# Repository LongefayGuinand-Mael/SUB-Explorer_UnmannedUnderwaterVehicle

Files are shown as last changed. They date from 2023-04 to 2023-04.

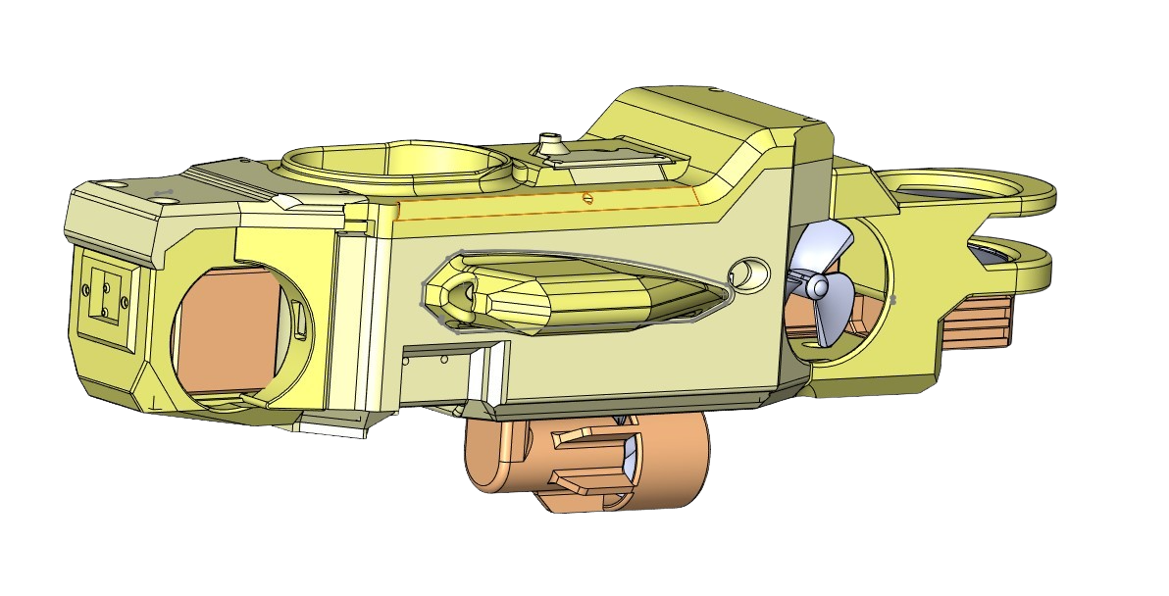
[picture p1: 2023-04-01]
UUV.png

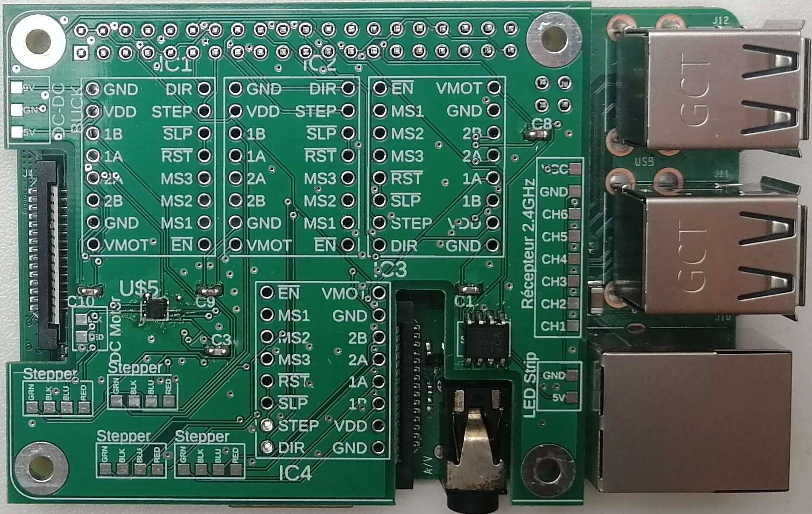
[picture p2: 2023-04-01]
SchémasÉlectroniques+PCB/Photos des PCB sur les Raspberry Pi/PCB Raspberry Pi 4B.jpg

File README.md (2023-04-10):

<br>
	<p align="center">
		<h1 align="center"> :warning:   WARNING   :warning: </h1>
	</p>
<br>

This project was made in French only for an Academic Work. So please consider that whole project files names, reports and other are only in French. This project was made during our last year in the ESME Sudria Engineering School between October 2022 and March 2023. 

Please note that this README.md is only a preface to all the work done during these 6 months of the project, if you wish to know more after reading this README, please refer to our report `/Rapports/Rapport Projet Drone Sous-Marin.pdf` (written in French).

------------------------------------------------------
------------------------------------------------------

<br>
	<p align="center">
	    <h1 align="center">Unmanned Underwater Vehicle - Sub-Explorer</h1>
	</p>
</br>

Dans le cadre de notre dernière année academic d'ingénierie à l'ESME Sudria (Master 2), mon groupe et moi-même avons travaillé pendant une durée de 6 mois sur un drone sous-marin ayant pour objectif principal la recherche scientifique. Dans le cadre de notre projet, nous avons mis en place diverses choses afin de mener à bien cet objectif et nous sommes arrivé à un résultat très concluant. Veuillez à noter que le README.md n'est qu'une préface à tout le travail effectué lors de ces 6 mois de projet, si vous avez pour souhait de d'en savoir plus après lecture de ce README, veuillez à vous référer à notre rapport `/Rapports/Rapport Projet Drone Sous-Marin.pdf`.

Ce projet c'est principalement articulé avec les parties suivantes :
- Définition du Cahier des charges 
- Veille technologique :
	- Recherche des Composants
	- Mise en place d'un schéma électrique
	- Réalisation des Printed Circuit Board
- Programmation (Python)
- Modélisation structurelle 3D du drone   
*Les autres parties (moins techniques) sont trouvables dans le rapport complet de notre projet de fin d'études.*

------------------------------------------------------

### Sommaire :
1. [Définition du Cahier des Charges](#cahier-des-charges)
2. [Choix des Composants](#choix-composants)
3. [Schémas Électroniques](#schémas-électroniques)
4. [Réalisation des Printed Circuit Board (PCB)](#pcb)
5. [Programmation](#programmation)
6. [Modélisation structurelle du drone](#modélisation-3d)
7. [Noms et Contacts des étudiants ayant travaillé sur le projet](#contacts)

------------------------------------------------------

<br>
	<p align="center">
	    <h2 align="center">Définition du Cahier des Charges</h2>
	</p>
</br>

### Introduction :
Notre objectif est de concevoir un drone sous-marin dans son intégralité, allant de la définition du cahier des charges à sa conception électronique et  3D. Pour mettre à bien notre projet, l'objectif premier est de mettre au point un système de pilotage efficace pour notre drone sous-marin, en veillant à sa motorisation directionnelle, à sa radiocommunication et à son design 3D. Nous prévoyons également d'intégrer des outils scientifiques à notre plateforme, ainsi que de travailler sur une optimisation de son design. En somme, ce projet est l'opportunité pour nous de mettre en pratique nos connaissances en matière de systèmes embarqués, tout en nous confrontant à des défis technologiques passionnants.
Dans le cadre de ce projet, nous mettons d’abord la priorité sur le pilotage de la plateforme (motorisation directionnelle, radiocommunication). Les outils scientifiques et l’optimisation du design seront vus dans un second temps.

### Fonctionnalités :
1. _Les fonctionnalités primaires :_
	- UUV manœuvrable sur 3 dimensions. → Motorisation directionnelle (lacet, tangage, profondeur, direction).
	- L’UUV est radiocommandé. → Conception d’un flotteur permettant de maintenir l’antenne (récepteur 2.4GHz) hors de l’eau afin de simplifier la communication entre le système de pilotage et la machine.
→ Utilisation d’une télécommande et d’un récepteur 2.4GHz.
	- Le drone doit être étanche afin de protéger le système de l’eau.
	- Le drone doit également répondre à une limite de taille afin qu'il puisse se déplacer dans des espaces restreints. Nous avons donc pour objectif de taille que le drone fasse maximum 600 mm de longueur et 300 mm de diamètre.
	- La flottaison de l’UUV doit être neutre : nous devons faire en sorte d’obtenir un équilibre entre le poids et la poussée d’Archimède du drone.
	- Nous voulons que le drone puisse effectuer des missions scientifiques d’une durée minimum de 30 minutes - 1 heure. Cela nous défini une contrainte d'autonomie.
2. _Les fonctionnalités secondaires :_
	- Retour vidéo (mise en place d’une caméra embarquée pour pouvoir voir ce qui se trouve dans l’environnement du drone même lorsque celui-ci n'est pas visible depuis la surface).
	- Système d’éclairage LED afin de pouvoir voir convenablement l’environnement où se trouve le drone via le retour caméra.
	- Capteurs de température et de pression (utile pour de la recherche et pour assurer le maintien structurel du drône en fonction de la pression exercée sur lui de part la pression de l’eau - liée à la profondeur à laquelle il se trouve).
	- Structure résistante aux chocs et protégeant les composants fragiles pouvant être exposés à l’extérieur du drone (par exemple les capteurs ou encore les hélices des moteurs).
3. _Les fonctionnalités intéressantes supplémentaires :_
	- Ajout de systèmes pour la collecte de données scientifiques : échantillonneur, sondeur, GPS, divers nouveau capteur, etc.
	- Intégrer une capacité de stockage et de récupération rapide des données.
	- Développement d’une application mobile pour le pilotage de tout le drone (contrôle de
son déplacement dans l’espace et des éléments scientifiques qu’il embarque et permettant l’affichage du flux vidéo en temps réel).

### Schéma Bloc Fonctionnel du Projet :

SchémaBlocFonctionel

------------------------------------------------------

<br>
	<p align="center">
	    <h2 align="center">Choix des Composants</h2>
	</p>
</br>

*Toutes les datasheets des composants utilisés sont regroupées dans les fichiers du projet dans le dossier `/DatasheetsComposents`.*

### Intelligences Numériques :
Nous utilisons dans ce projet 2 Raspberry Pi.   
- La première est une **Rasberry Pi 4B (de 4 à 8 Go RAM)**. Cette Raspberry Pi nous permet la réception des données envoyées par la télécommande et donc par l'utilisateur afin de contrôler les moteurs et l'allumage ou non des LED qu'il embarque.   
- La seconde est une **Raspberry Pi 3B+**. Cette Raspberry Pi, quant-à elle, nous permet d'éberger un WebServeur local afin d'avoir un retour caméra et capteurs (afin de connaître, même si nous ne voyons plus le drone depuis la surface, de connaître l'environnement dans lequel il est).

### Caméra Embarquée :
Comme dit plus haut, nous avons besoin de savoir consatemment l'environnement du drone même lorsque celui-ci n'est pas visible depuis la surface. Ainsi, nous utilisons une caméra embarquée dans le drone. Par soucis de simplicité et surtout de qualité, nous avons choisi de prendre la **Camera Module V2 Raspberry** (existe maintenant également avec un autofocus). Cette caméra embarqué nous permet d'avoir une excélente qualité (1280x720 pixel) avec un haut débit (jusqu'à 24 fps) et puis elle est nativement supportée par la Rasberry Pi 3B+ qui va l'utiliser et envoyer son stream vidéo sur le WebServeur qu'elle host.

### Récepteur Radio + Télécommande :
Dans notre projet, nous avons eu la volonté de contrôler notre drone à distance en imaginant un moyen d'éviter d'avoir un drone qui embarque un enrouleur de câble pour pouvoir communiquer avec l'utilisateur via ce qui s'apparente à un câble d'Arianne. Ainsi, nous avons choisi de mettre en place ce câble d'Arianne entre notre sous-marin et un flotteur. Ce flotteur pourra ainsi embarquer 2 antennes. L'une étant l'antenne radio (2.4GHz) et l'autre une antenne WiFi (dont nous reparlerons plus tard).

Nous avons donc prit un récepteur radio **FS-IA6B**. Ce récepteur 2.4GHz (fréquence laissée libre pour la science et d'autres recherche) va nous servirà communiquer avec notre sous-marin. En plus de ce récepteur, nous avons une télécommande FlySky (utilisée dans le modélisme et qui convient très bien à notre projet pour le moment). 

### Composants ayant un lien avec le déplacement du drone :
La phase la plus technique dans ce projet est le déplacement du sous-marin car en plus de la réception des données de la télécommande redio, il faut adapter les données récupérées en données fiables pour contrôler convenablement nos moteurs. 

Nous avons 2 types de moteurs : 
- 4 moteurs pas-à-pas **17HS08-1004S** commandé à l'aide d'un driver moteur **A4988-1182** par la Raspberry Pi 4B.
- 1 moteur à courant continu de la marque **lichifit** (utilisé dans le modélisme naval) commandé à l'aide d'un driver moteur **DRV8838** également par la Raspberry Pi 4B.

Les moteurs pas-à-pas seront utilisés pour des mouvements plus précis tels que les mouvements translatifs lattéraux et de profondeur et pour les mouvement rotatifs (lacet et tangage).    
Le moteur à courant continu sera quant-à lui utilisé uniquement pour la translation avant-arrière et sera notre propulseur principal.

### Composants ayant un lien avec la récupération de données (capteurs) :
Dans notre sous-marin, nous souhaiton à minima pouvoir récupérer deux données, la température et la pression. 

Pour le capteur de température, nous avons choisi le capteur **DS18B20**. Le choix de ce composant à été assez intuitif puisque celui-ci ressemble à une sonde, il est étanche et à une plage d'utilisation large avec une précision de 0.0625°C.

Pour le capteur de pression, nous avons choisi le capteur **MS5837-30BA**. Ce capteur fonctionne en I²C, il est étanche et a une plage de fonctionnement allant jusqu'à 30 bar (jusqu'à 290m de profondeur dans l'eau) avec une précision de 0.2mBar (soit ±2mm).

À l'avenir, nous imaginons pouvoir rajouter des capteurs tels que celui de salénité de l'eau et de pollution maritime ou encore un capteur de tangage pour la stabilisation du drone.

### Composants autres :
Les autres composants sont divers. 

Nous avons ici un convertisseur Buck-Boost **DFR0753** afin de pouvoir allimenter d'une tension de 5V les 2 Raspberry Pi mais d'une tension de 9V les différents moteurs et le bandeau LED.

En parlant du **bandeau LED**, nous avons imaginé embarquer des LED dans le sous-marin afin de permettre de les activer ou non pour pouvoir, en toutes circonstances et sur demande de l'utilisateur, de voir l'environnement de travail du drone sous-marin qu'il soit visible depuis la surface ou pas. Le bandeau LED est unicolore blanc, certifié IP67 (étanche poussière et eau), et peut être allimenté jusqu'à 12V. Nous l'utilisons avec une tension d'allimentation de 9V largement suffisante pour nous.

------------------------------------------------------

<br>
	<p align="center">
	    <h2 align="center">Schémas Électroniques</h2>
	</p>
</br>

*Pour une meilleure qualité, les images des schémas électroniques sont trouvables dans les fichiers du projet dans le dossier `/SchémasÉlectroniques+PCB`) Leurs noms étants : `Schéma Électronique - Raspberry Pi 3B+.png` et `Schéma Électronique - Raspberry Pi 4B.png`.*

Après l'analyse de tous les composants, nous avons mis en place 2 schémas électroniques. L'un concerne la Raspberry Pi 3B+ et l'autre la Raspberry Pi 4B.

### Partie Raspberry Pi 3B+ :

Pour cette partie, nous retrouvons dans le schéma électronique les capteurs de température et de pression. Il est à noté également que nous avons de géré par cette Raspberry Pi la caméra embarquée.

Schéma Électronique - Raspberry Pi 3B+

### Partie Raspberry Pi 4B :

Pour cette partie, nous retrouvons dans le schéma électronique les 4 moteurs pas-à-pas ainsi que leurs drivers respectifs, le moteur à courant continu et son driver, le bandeau LED, le récepteur 2.4GHz et des pins de branchement pour le convertisseur Buck-Boost (9V à 5V). 

Schéma Électronique - Raspberry Pi 4B

***À Noter :*** *Les fichiers Fusion360 ayants permis de faire les schémas électroniques ainsi que les PCB sont trouvables dans les fichiers du projet dans le dossier `/SchémasÉlectroniques+PCB/FichiersFusion`.*

------------------------------------------------------

<br>
	<p align="center">
	    <h2 align="center">Réalisation des Printed Circuit Board (PCB)</h2>
	</p>
</br>

*Fichiers de conception des PCB sont trouvables dans les fichiers du projet dans le dossier `/SchémasÉlectroniques+PCB/FichiersConceptionPCB`. Un dossier regroupe les fichiers utiles par un fabriquant de PCB pour faire celui de la Raspberry Pi 3B+ et un autre dossier est pour celui de la Raspberry Pi 4B.*

Cette partie ne pourra pas être beaucoup développée à l'écrit. Pour faire au plus simple, suite à la mise en place de nos 2 schémas électroniques, nous avons pu mettre en place 2 PCB qui seront utilisés pour notre projet (un pour chacune des intelligences électroniques). Sur le PCB de la Raspberry Pi 3B+ on peut y retrouver les branchements des différents capteurs tandis que sur le PCB de la Raspberry Pi 4B on y retrouve tous les composants utiles pour la réceptions des commandes de l'utilisateurs et les différents systèmes et branchements pour les moteurs et bandeau LED (en outre, tout ce qui est contrôllable par l'utilisateur à distance). 

La seconde chose importante mise en place est la définition de contraintes de dimentionnement afin de permettre aux 2 PCB de se brancher directement sur les Raspberry Pi. Ces contraintes sont principalement liée aux composants internes des Raspberry Pi et leurs hauteurs qui peuvent être génantes (dans les grandes lignes, ça regroupe les composants tels que celle du port éthernet, des ports USB, port de branchement caméra, port Jack et HDMI).

***Rappel :*** *Les fichiers Fusion360 ayants permis de faire les schémas électroniques ainsi que les PCB sont trouvables dans les fichiers du projet dans le dossier `/SchémasÉlectroniques+PCB/FichiersFusion`.*

------------------------------------------------------

<br>
	<p align="center">
	    <h2 align="center">Programmation (Python)</h2>
	</p>
</br>

*Tous les fichiers de programmation sont regroupées dans les fichiers du projet dans le dossier `/Programmation/Code`. Dans ce dossier on peut y retrouver les codes en Python (`.py`) ainsi que des logigrammes des programmes (au format `.png`).* 

Pour commencer, nous avons 2 intelligences numériques (1 Raspberry Pi 3B+ & 1 Raspberry Pi 4B) qui vont fonctionner simultannément mais de manière totalement distincte l'une de l'autre. Ainsi, nous exposons ci-dessous les logigrammes des programmes des 2 intelligences numériques : 

### Partie Raspberry Pi 3B+ :

Logigramme Raspberry Pi 3B+ - SUB-Explorer

Nous pouvons retrouver 2 étapes, l'initialisation et le fonctionnement. L'initialisation nous permet d'instancier les divers pins de la Raspberry que nous utilisons par la suite dans notre code ainsi que les multiples librairies utilisées. La phase de fonctionnement permet l'hébergement et l'envoie du stream de la caméra embarquée sur le WebServeur local de la Raspberry Pi 3B+. Il sera possible par la suite de créer un multi-thread afin de pouvoir récupérer en parallèle du WebServeur des données de capteurs pour les ajouter au retour caméra sur la page Web hébergée (*un début de code dans ce sens est retrouvable sous le nom `TempPrint_CameraWebLocal.py`*).

### Partie Raspberry Pi 4B :

Logigramme Pi4B (1) - SUB-Explorer

Tout comme pour la Raspberry Pi 3B+, nous pouvons y voir qu'il y a 2 étapes dans ce logigramme, l'initialisation et le fonctionnement en temps-réel avec la mise en place d'un multi-thread ce qui équivaut à l'utilisation de plusieurs coeurs du processeur de la Raspberry Pi 4B qui se charge de ce code. *On peut également retrouver le programme de récupération des données réceptionnées depuis la télécommande radio sur le logigramme `Logigramme Pi4B (2) - SUB-Explorer.png` mit dans le fichier `/Programmation/LogigrammesExplicatifs/`.*

------------------------------------------------------

<br>
	<p align="center">
	    <h2 align="center">Modélisation Structurelle du Drone</h2>
	</p>
</br>

Voici une image de l'assemblage total des pièces imprimées en 3D de notre drone : 

UUV

*Pour une meilleure qualité, l’image de l'assemblage de la modélisation structurelle du drone sont trouvables dans les fichiers du projet (au niveau de la racine). Son nom étant : `Assemblage3D.png`.*   

Voici également une vidéo montrant l'**ordre assemblage des quelques 28 pièces (_vis non-incluses_)** composants notre sous-marin : 

https://user-images.githubusercontent.com/80823327/229296633-9bad1075-d35f-4a4c-87c2-66e0a59497dc.mp4
   
**Concernant les fichiers 3D de chacune des pièces ainsi que de l'assemblage, ces fichiers sont trouvables dans les fichiers du projet dans le dossier `/Modélisation3D`.**

------------------------------------------------------

<br>
	<p align="center">
	    <h2 align="center">Noms et Contacts</h2>
	</p>
</br>


 
 

-------------------------------------
-------------------------------------
## License
***© COPYRIGHT - All Rights Reserved - Zapata Industry (LONGEFAY-PIOT-POPESCO)***  
***Important :*** *Afin de poursuivre le projet, merci de nous contacter sur LinkedIn pour avoir notre approbation.*

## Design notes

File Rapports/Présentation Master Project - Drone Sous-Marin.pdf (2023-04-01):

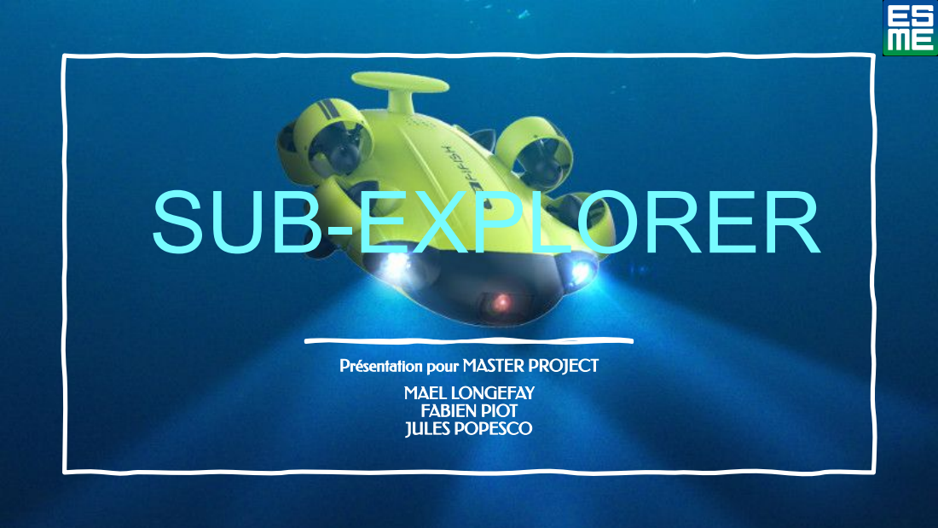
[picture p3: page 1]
SUB-EXPLORER; MAEL LONGEFAY FABIEN PIOT JULES POPESCO

Présentation pour MASTER PROJECT

# Sa mission :

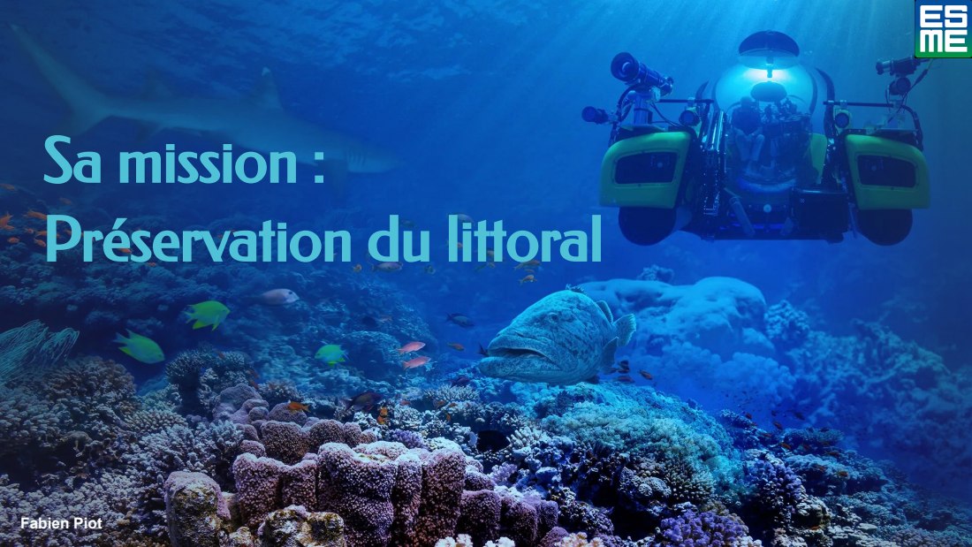
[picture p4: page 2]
Fabien Piot

Préservation du littoral

# Découvrez le drone sous-marin SUB-Explorer

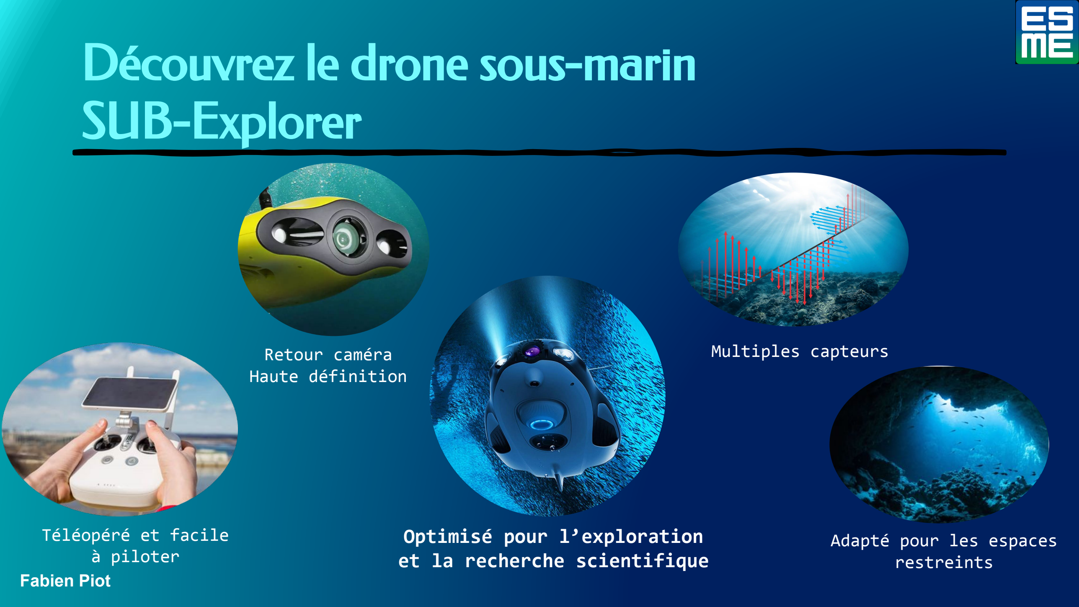
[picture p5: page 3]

Optimisé pour l’exploration et la recherche scientifique

Adapté pour les espaces
restreints

Téléopéré et facile
à piloter

Retour caméra
Haute définition

Multiples capteurs

Fabien Piot

# SUB-Explorer c’est également …

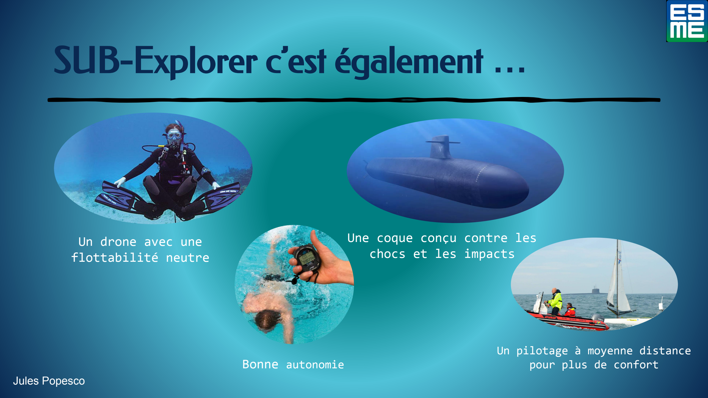
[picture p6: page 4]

Un drone avec une
flottabilité neutre

Bonne autonomie

Une coque conçu contre les chocs et les impacts

Un pilotage à moyenne distance pour plus de confort
Jules Popesco

# Voici à quoi ressemble notre prototype

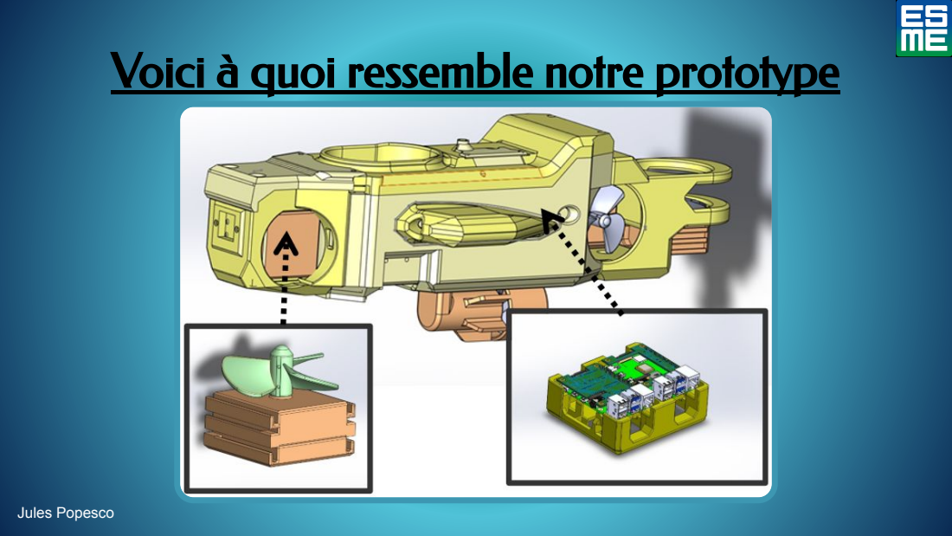
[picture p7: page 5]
Jules Popesco

# Montage du prototype

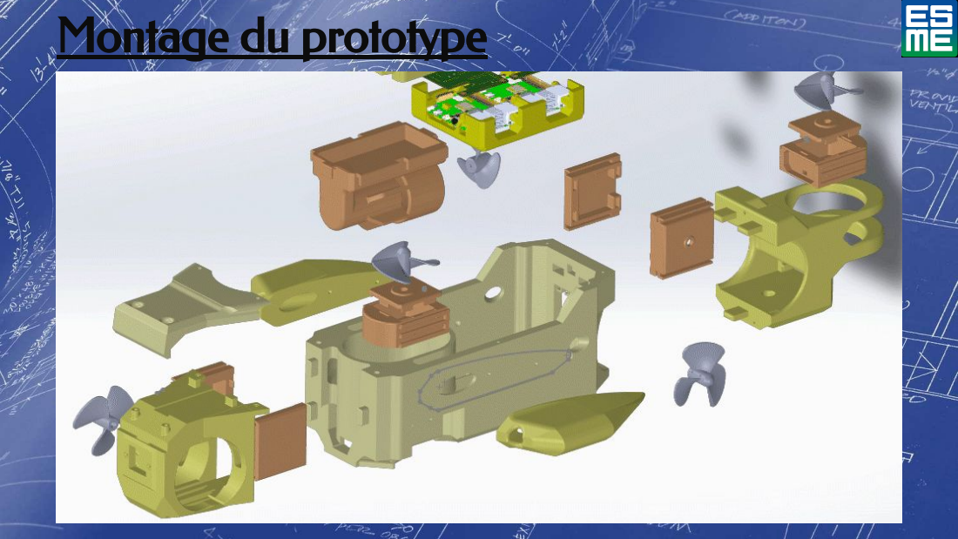
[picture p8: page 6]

# La force de SUB-Explorer : Sa grande modularité

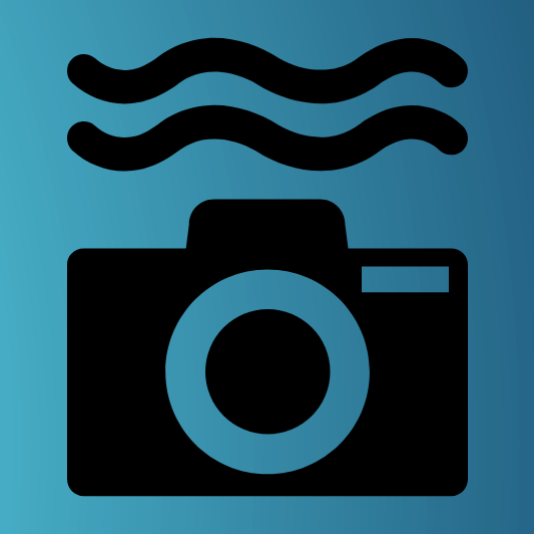
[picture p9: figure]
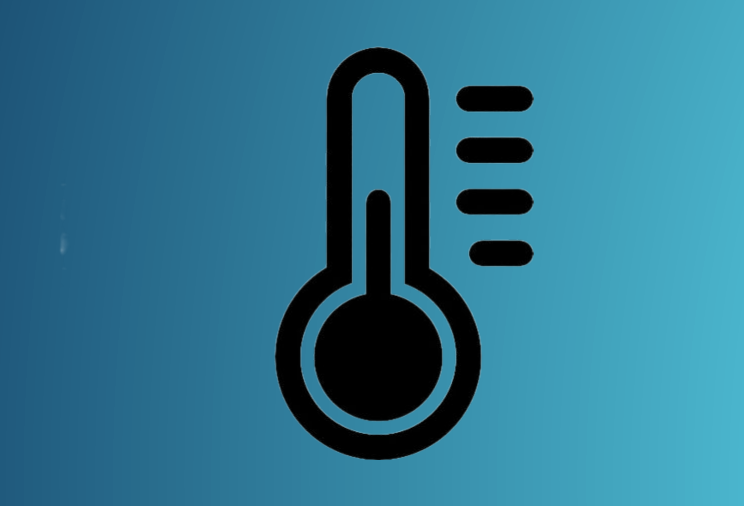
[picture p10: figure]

Plusieurs modules embarqués :

- caméra embarqué haute définition
- capteur de température

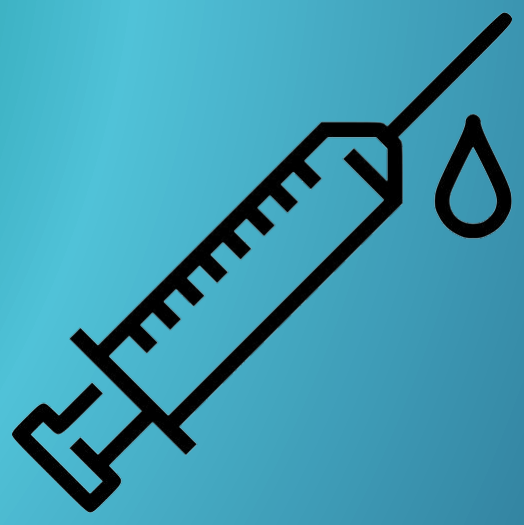
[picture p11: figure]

- capteur de pression

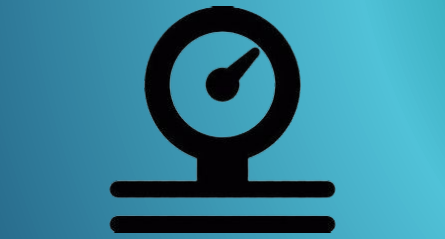
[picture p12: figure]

- module d'échantillonnage
- un éclairage LED

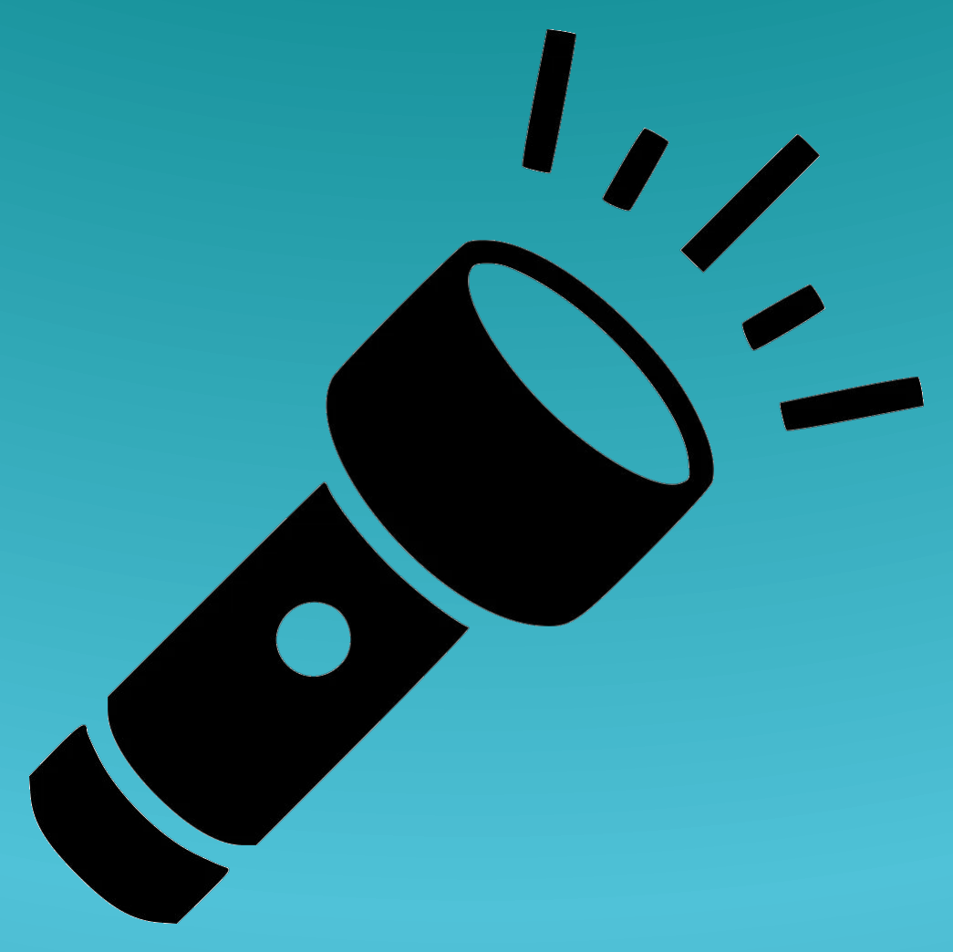
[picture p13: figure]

Mael LONGEFAY

# L’avenir de SUB-Explorer

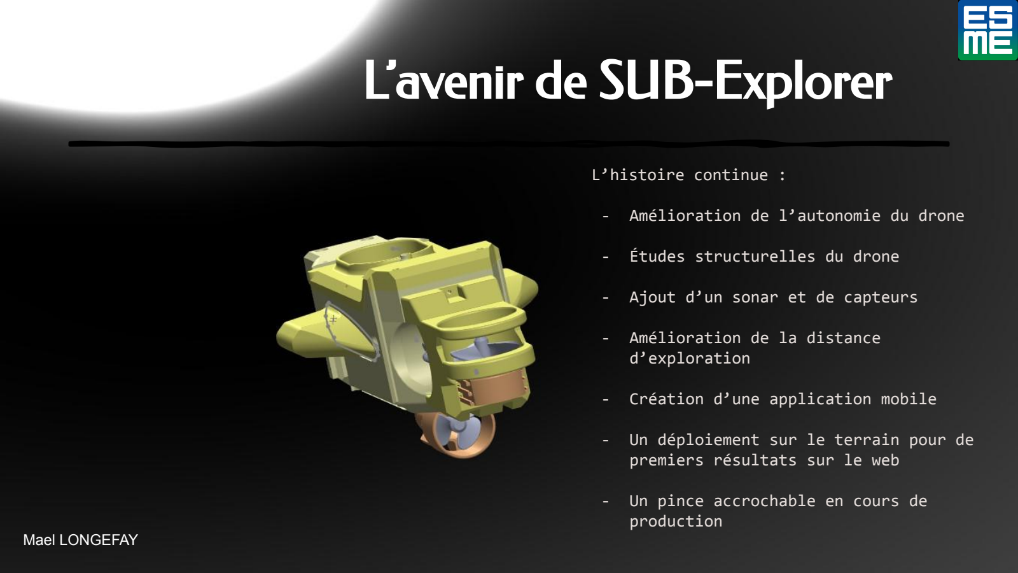
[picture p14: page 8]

L’histoire continue :

- Amélioration de l’autonomie du drone
- Études structurelles du drone
- Ajout d’un sonar et de capteurs
- Amélioration de la distance d’exploration
- Création d’une application mobile
- Un déploiement sur le terrain pour de premiers résultats sur le web
- Un pince accrochable en cours de production
Mael LONGEFAY

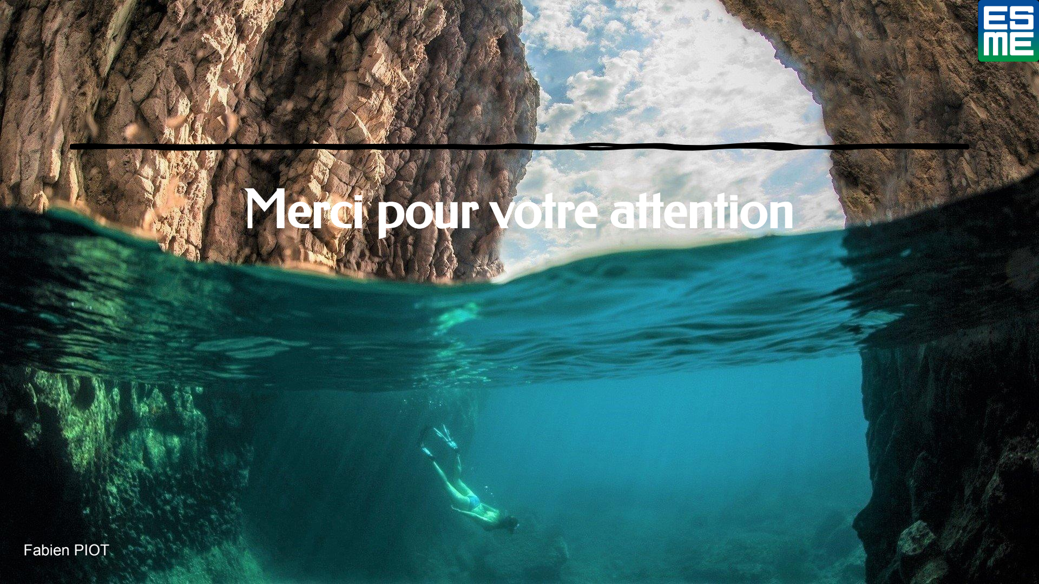
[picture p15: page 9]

# Merci pour votre attention

Fabien PIOT

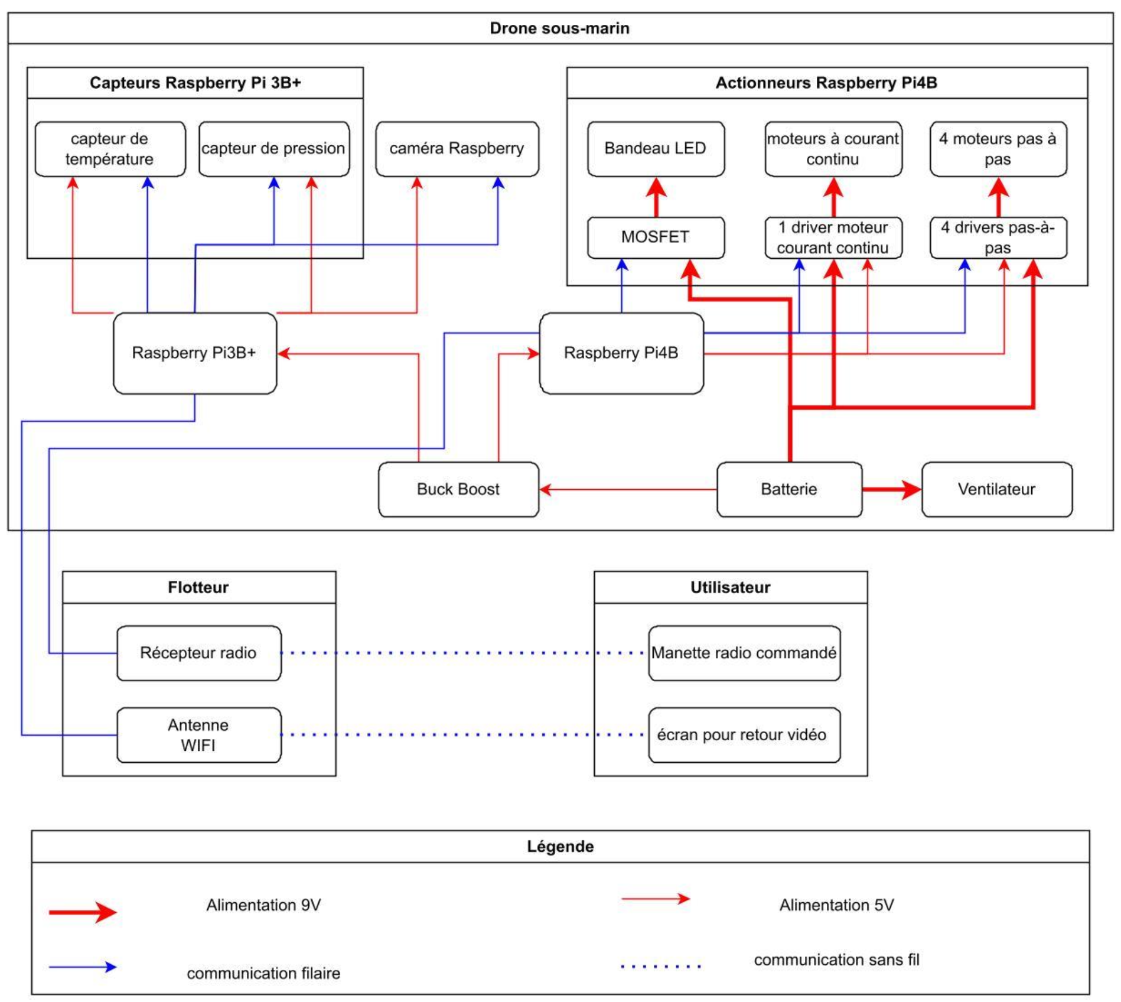
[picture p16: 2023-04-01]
SchémaBlocFonctionel.png

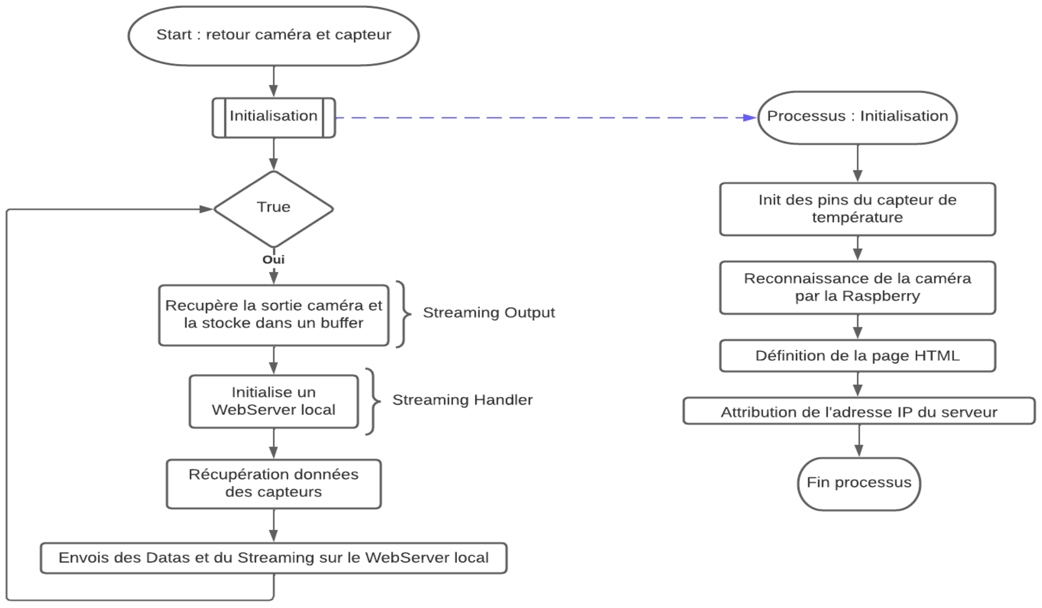
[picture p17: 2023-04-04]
Programmation/LogigrammesExplicatifs/Logigramme Raspberry Pi 3B+ - SUB-Explorer.png

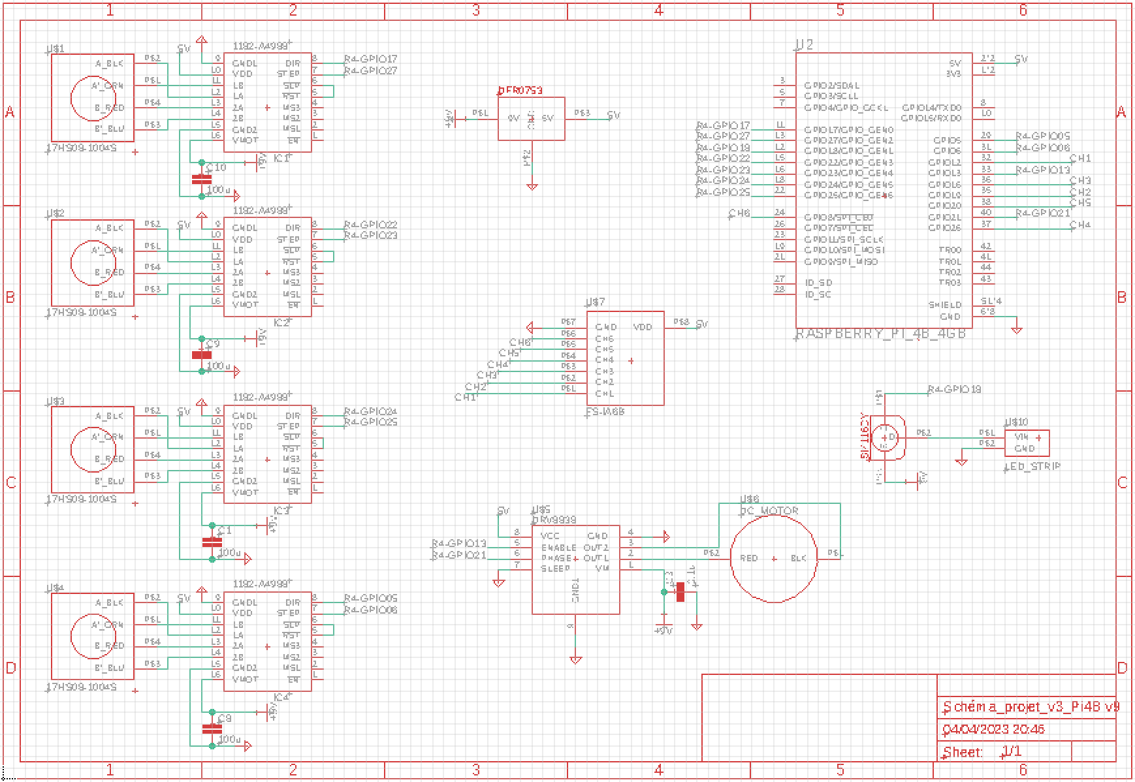
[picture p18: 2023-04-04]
SchémasÉlectroniques+PCB/Schéma Électronique - Raspberry Pi 4B.png

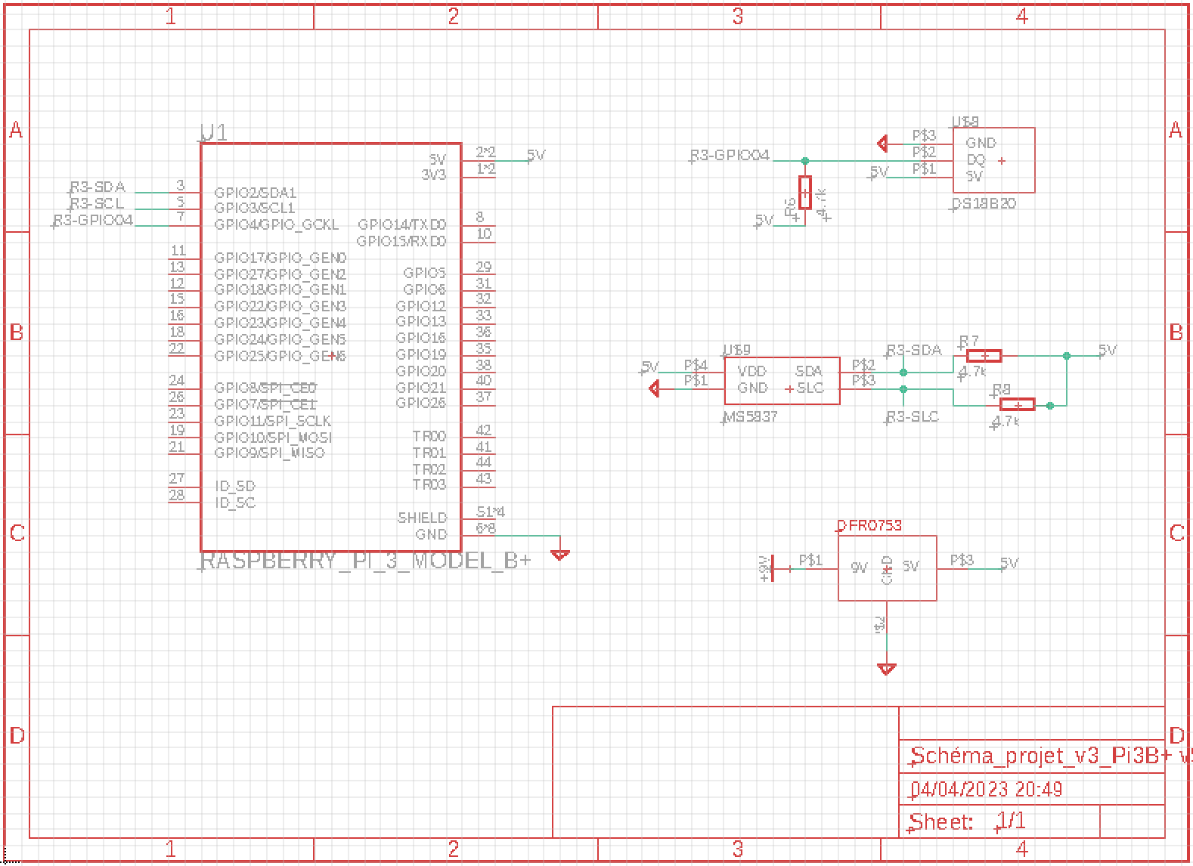
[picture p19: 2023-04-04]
SchémasÉlectroniques+PCB/Schéma Électronique - Raspberry Pi 3B+.png

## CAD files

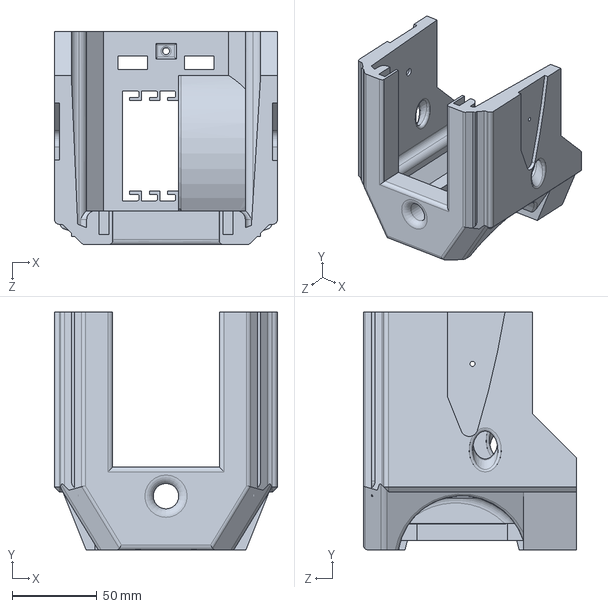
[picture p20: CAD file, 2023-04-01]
Modélisation3D/CoqueMain2.sldprt
131.8 x 140.5 x 126.0 mm

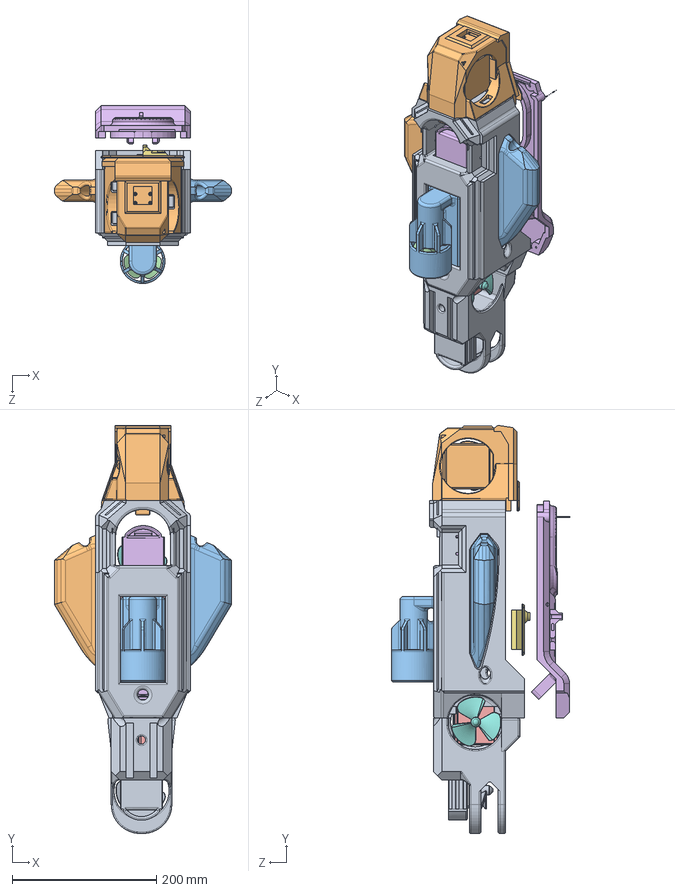
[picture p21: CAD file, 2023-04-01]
Modélisation3D/Assemblage1.sldasm
245.8 x 565.2 x 246.8 mm
CoqueMain
Aile
AileGauche
blk_steplarge_under
blk_steplarge_upper
bloc_moteur_step_under
bloc_moteur_step_upper
Helice x 2
Blk_ariere
Blk_avant
bloc_moteurCC
Helice DC
Etagère
Couverclehull
Couverclehull_ant

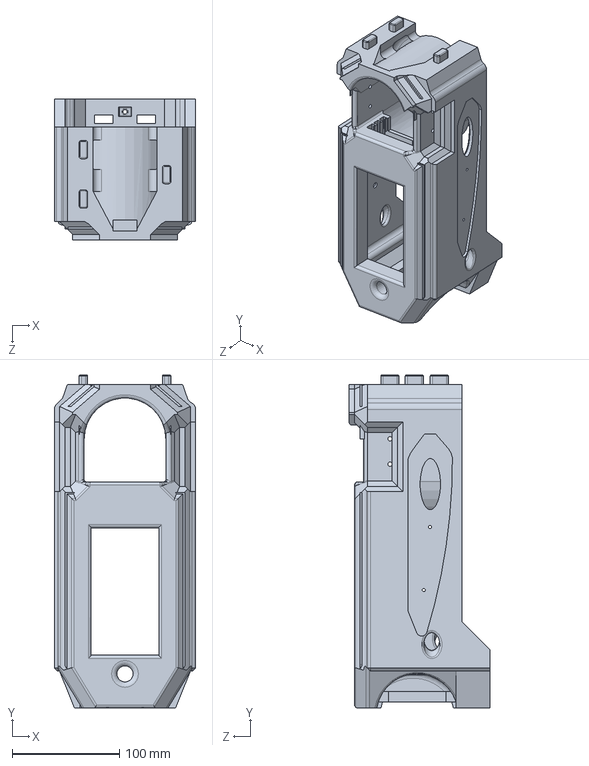
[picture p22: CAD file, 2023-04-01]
Modélisation3D/CoqueMain.sldprt
131.8 x 310.2 x 131.0 mm

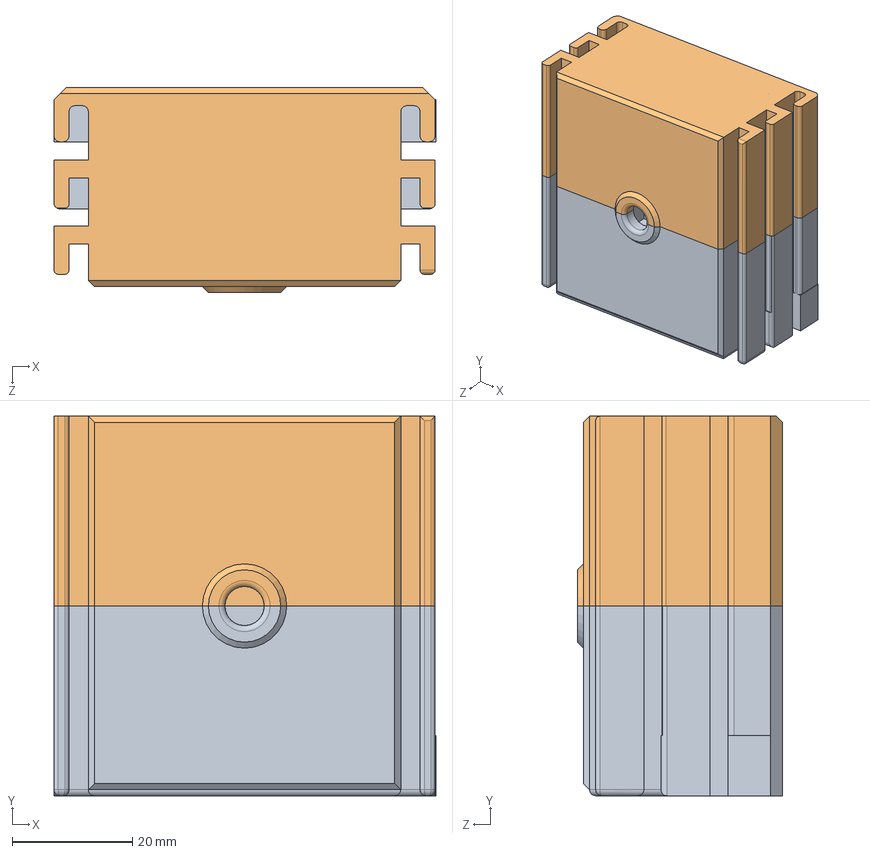
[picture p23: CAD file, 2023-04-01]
Modélisation3D/Stepmotlarge.sldasm
63.4 x 63.0 x 34.0 mm
blk_steplarge_upper
blk_steplarge_upper2

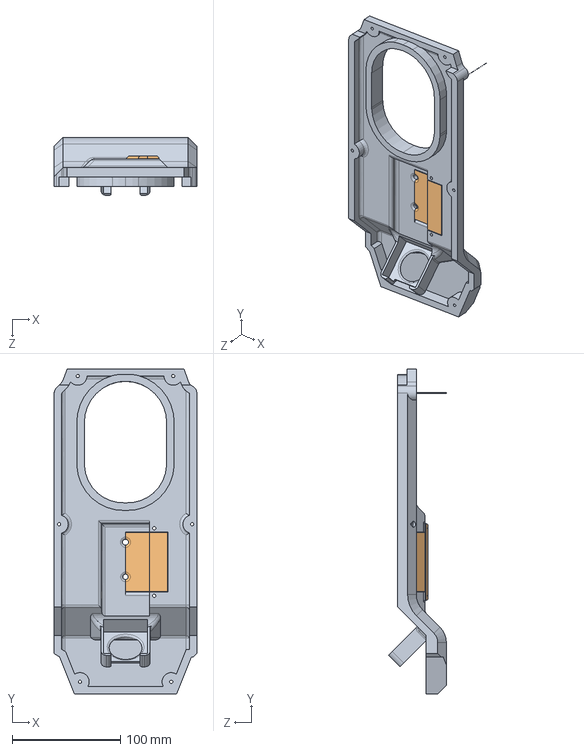
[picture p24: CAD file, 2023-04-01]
Modélisation3D/Assemblage2.sldasm
131.8 x 300.2 x 53.4 mm
Couverclehull
Couverclehull_ant

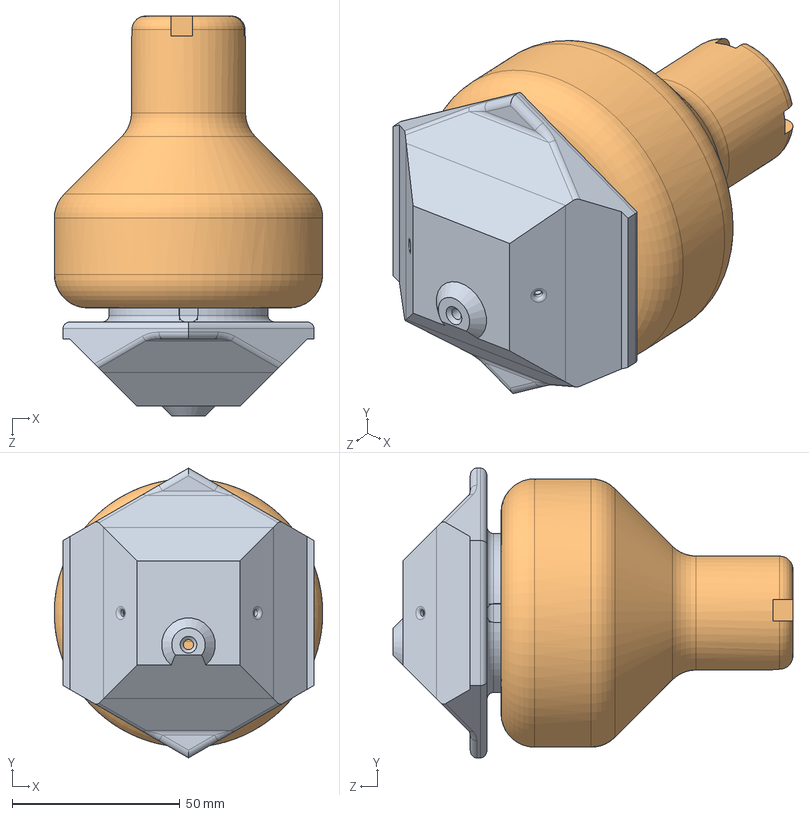
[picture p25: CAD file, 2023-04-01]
Modélisation3D/FlotteurAssemblage.sldasm
80.0 x 86.3 x 119.2 mm
Couvercle flotteur
Flotteur2

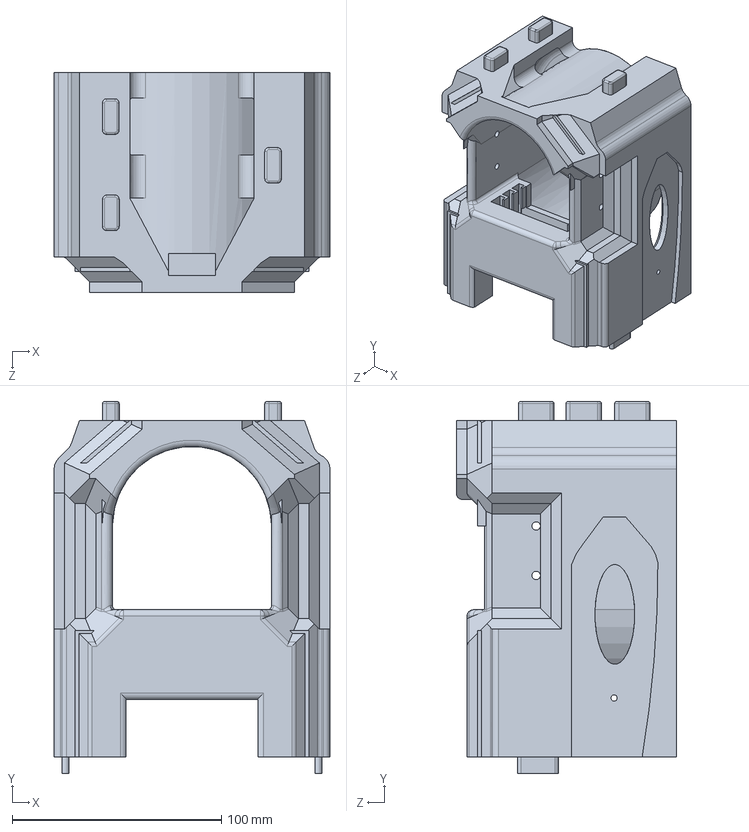
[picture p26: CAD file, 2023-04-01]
Modélisation3D/CoqueMain1.sldprt
131.8 x 177.7 x 105.0 mm

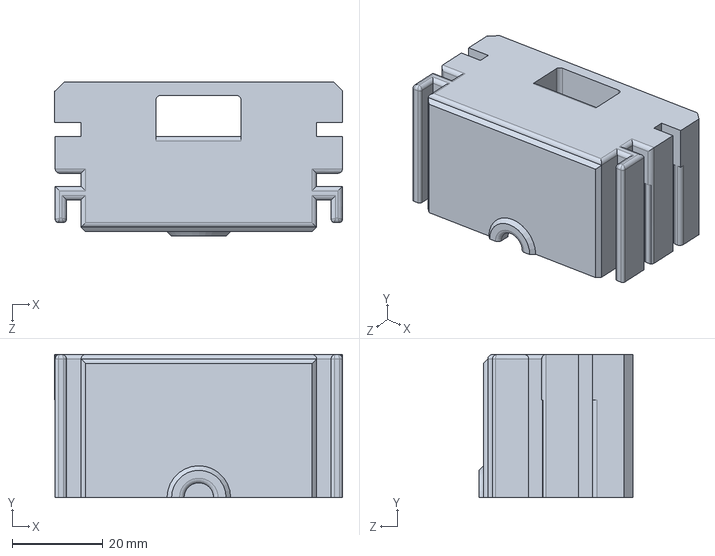
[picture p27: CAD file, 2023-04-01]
Modélisation3D/NewBLK.sldprt
63.4 x 31.5 x 34.0 mm

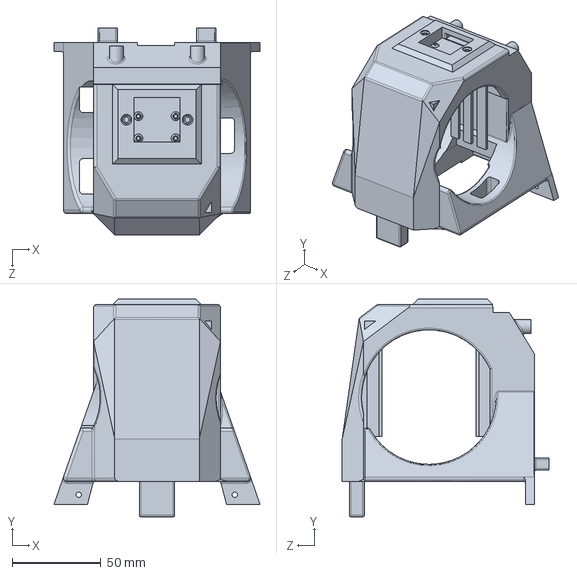
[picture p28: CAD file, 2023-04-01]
Modélisation3D/CoqueAvant.sldprt
116.3 x 123.0 x 116.7 mm

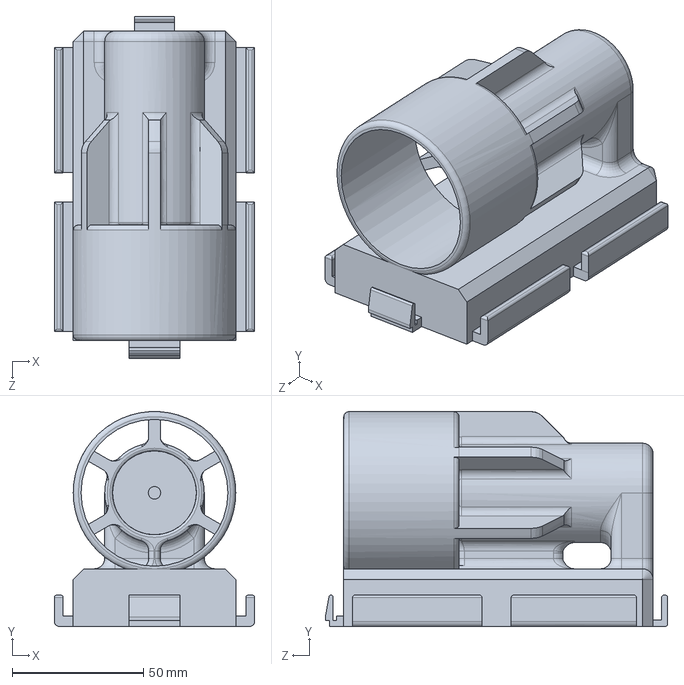
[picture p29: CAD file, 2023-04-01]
Modélisation3D/bloc_moteurCC.sldprt
76.4 x 82.0 x 130.6 mm

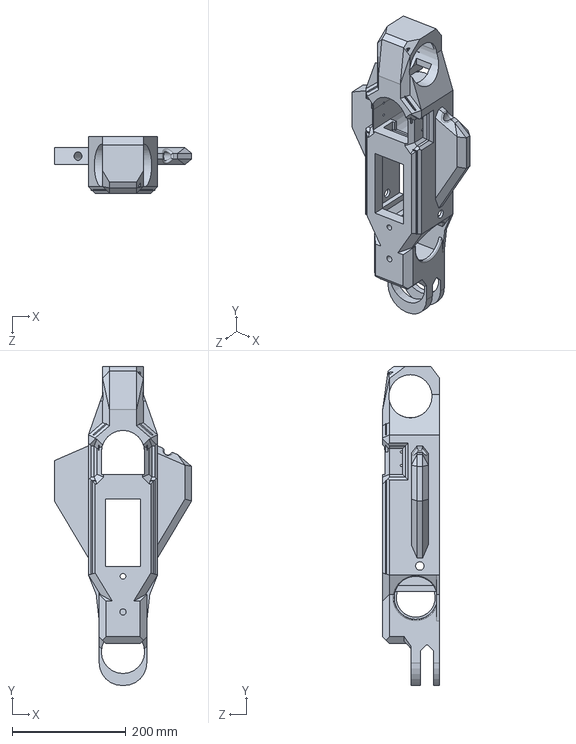
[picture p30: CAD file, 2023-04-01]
Modélisation3D/Coque1.sldprt
241.8 x 561.5 x 100.0 mm

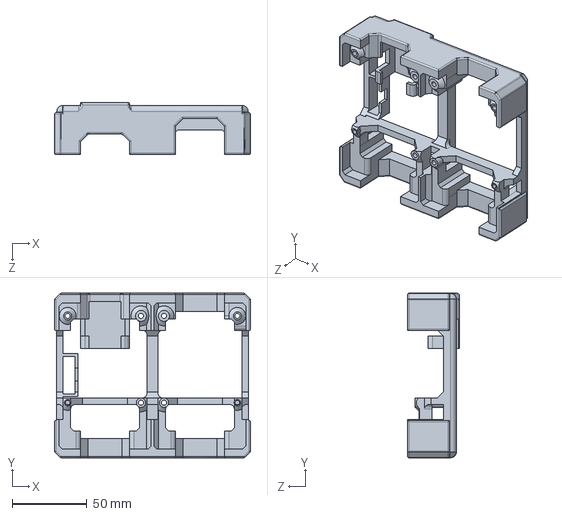
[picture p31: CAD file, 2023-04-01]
Modélisation3D/Etagère.sldprt
131.0 x 110.0 x 34.7 mm

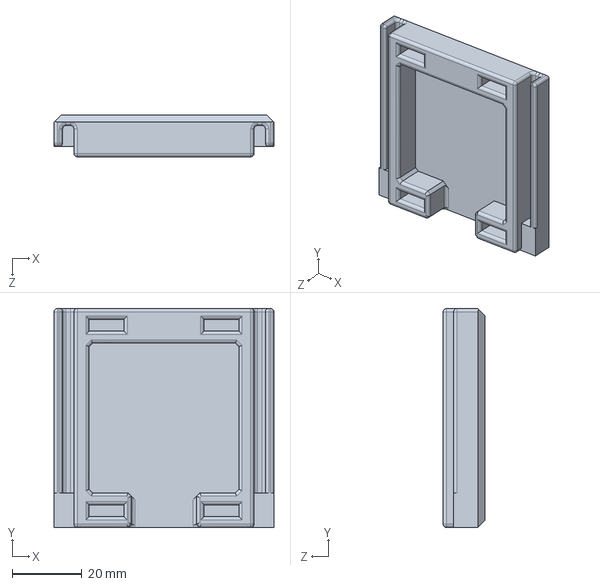
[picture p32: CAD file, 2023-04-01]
Modélisation3D/blk_steplarge_under2.sldprt
63.3 x 63.0 x 12.0 mm

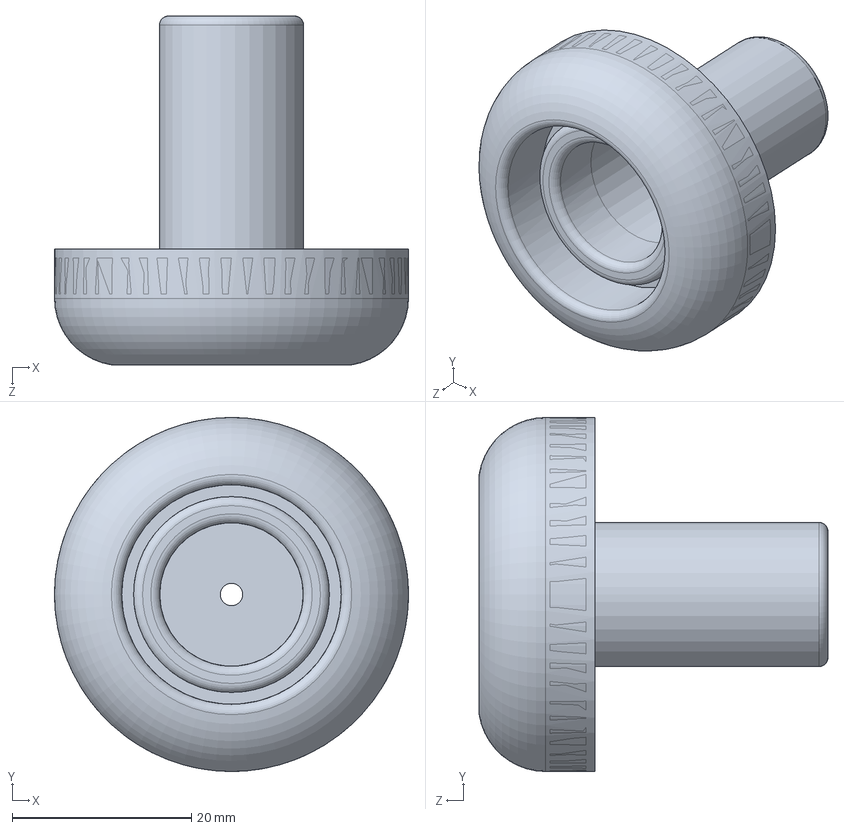
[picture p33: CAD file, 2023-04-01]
Modélisation3D/FlotteurTest-v3.sldprt
39.5 x 39.5 x 38.9 mm

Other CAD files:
Modélisation3D/Blk_ariere.sldprt
Modélisation3D/Helice.sldprt
Modélisation3D/blk_steplarge_under.sldprt
Modélisation3D/Couverclehull1_1.sldprt
Modélisation3D/Aile.sldprt
Modélisation3D/AileGauche.sldprt
Modélisation3D/Blk_avant.sldprt
Modélisation3D/CoqueArrière.sldprt
Modélisation3D/CoqueAvantCouv.sldprt
Modélisation3D/Couvercle-flotteur.sldprt
Modélisation3D/Couverclehull.sldprt
Modélisation3D/Couverclehull1.sldprt
Modélisation3D/Couverclehull1_2.sldprt
Modélisation3D/Couverclehull2.sldprt
Modélisation3D/Couverclehull_ant.sldprt
Modélisation3D/Flotteur2.sldprt
Modélisation3D/Helice-DC.sldprt
Modélisation3D/Newblk2.sldprt
Modélisation3D/PCB-3D_Pi3B.sldprt
Modélisation3D/Pièce1.sldprt
Modélisation3D/bloc_moteur_step_under.sldprt
Modélisation3D/bloc_moteur_step_upper.sldprt

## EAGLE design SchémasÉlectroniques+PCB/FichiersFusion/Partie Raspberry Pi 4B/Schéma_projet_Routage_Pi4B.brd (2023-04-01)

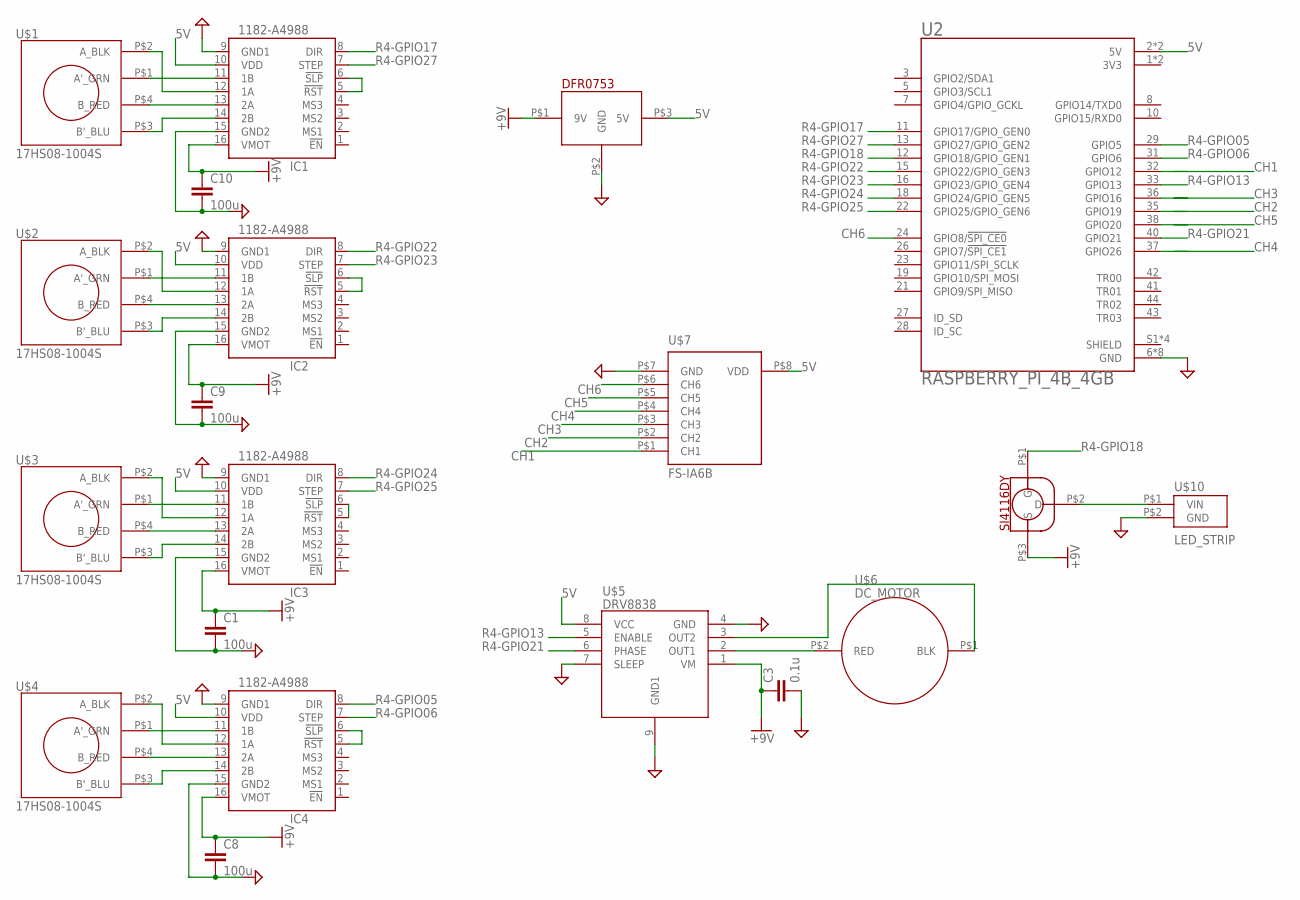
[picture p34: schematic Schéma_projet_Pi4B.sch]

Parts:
C1, C8, C9, C10: 100u; C0603
C3: 0.1u; C0603
IC1, IC2, IC3, IC4: 1182-A4988; A4988
U2: RASPBERRY_PI_4B_4GB; MODULE_RASPBERRY_PI_4B_4GB
U$1, U$2, U$3, U$4: 17HS08-1004S
U$5: DRV8838
U$6: DC_MOTOR
U$7: FS-IA6B
U$8: SI4116DY
U$10: LED_STRIP
U$11: DFR0753

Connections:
3V3: U2.1 (3V3), U2.17 (3V3)
5V: IC1.10 (VDD), IC2.10 (VDD), IC3.10 (VDD), IC4.10 (VDD), U2.2 (5V), U2.4 (5V), U$5.8 (VCC), U$7.P$8 (VDD), U$11.P$3 (5V)
+9V: C1.1, C8.1, C9.1, C10.1, IC1.16 (VMOT), IC2.16 (VMOT), IC3.16 (VMOT), IC4.16 (VMOT), U$8.P$3 (S), U$11.P$1 (9V)
AGND: C1.2, C3.2, IC2.9 (GND1), IC3.9 (GND1), IC3.15 (GND2), IC4.9 (GND1), U2.6 (GND), U2.9 (GND), U2.14 (GND), U2.20 (GND), U2.25 (GND), U2.30 (GND), U2.34 (GND), U2.39 (GND), U$5.4 (GND), U$5.7 (SLEEP), U$5.9 (GND1), U$7.P$7 (GND), U$10.P$2 (GND), U$11.P$2 (GND)
CH1: U$7.P$1 (CH1)
CH2: U$7.P$2 (CH2)
CH3: U$7.P$3 (CH3)
CH4: U$7.P$4 (CH4)
CH5: U$7.P$5 (CH5)
CH6: U2.24 (GPIO8/!SPI_CE0!), U$7.P$6 (CH6)
unnamed: C8.2, IC4.15 (GND2)
unnamed: U$5.3 (OUT2), U$6.P$1 (BLK)
unnamed: U$5.2 (OUT1), U$6.P$2 (RED)
unnamed: IC1.12 (1A), U$1.P$2 (A_BLK)
unnamed: IC1.11 (1B), U$1.P$1 (A'_GRN)
unnamed: IC1.13 (2A), U$1.P$4 (B_RED)
unnamed: IC1.14 (2B), U$1.P$3 (B'_BLU)
unnamed: IC2.12 (1A), U$2.P$2 (A_BLK)
unnamed: IC2.11 (1B), U$2.P$1 (A'_GRN)
unnamed: IC2.13 (2A), U$2.P$4 (B_RED)
unnamed: IC2.14 (2B), U$2.P$3 (B'_BLU)
unnamed: IC3.12 (1A), U$3.P$2 (A_BLK)
unnamed: IC3.11 (1B), U$3.P$1 (A'_GRN)
unnamed: IC3.13 (2A), U$3.P$4 (B_RED)
unnamed: IC3.14 (2B), U$3.P$3 (B'_BLU)
unnamed: IC4.12 (1A), U$4.P$2 (A_BLK)
unnamed: IC4.11 (1B), U$4.P$1 (A'_GRN)
unnamed: IC4.13 (2A), U$4.P$4 (B_RED)
unnamed: IC4.14 (2B), U$4.P$3 (B'_BLU)
unnamed: C3.1, U$5.1 (VM)
unnamed: U$8.P$2 (D), U$10.P$1 (VIN)
unnamed: IC4.5 (!RST), IC4.6 (!SLP)
unnamed: IC3.5 (!RST), IC3.6 (!SLP)
unnamed: IC2.5 (!RST), IC2.6 (!SLP)
unnamed: IC1.5 (!RST), IC1.6 (!SLP)
unnamed: C10.2, IC1.15 (GND2)
unnamed: C9.2, IC2.15 (GND2)
R4-GPIO05: IC4.8 (DIR), U2.29 (GPIO5)
R4-GPIO06: IC4.7 (STEP), U2.31 (GPIO6)
R4-GPIO13: U2.33 (GPIO13), U$5.5 (ENABLE)
R4-GPIO17: IC1.8 (DIR), U2.11 (GPIO17/GPIO_GEN0)
R4-GPIO18: U2.12 (GPIO18/GPIO_GEN1), U$8.P$1 (G)
R4-GPIO21: U2.40 (GPIO21), U$5.6 (PHASE)
R4-GPIO22: IC2.8 (DIR), U2.15 (GPIO22/GPIO_GEN3)
R4-GPIO23: IC2.7 (STEP), U2.16 (GPIO23/GPIO_GEN4)
R4-GPIO24: IC3.8 (DIR), U2.18 (GPIO24/GPIO_GEN5)
R4-GPIO25: IC3.7 (STEP), U2.22 (GPIO25/GPIO_GEN6)
R4-GPIO27: IC1.7 (STEP), U2.13 (GPIO27/GPIO_GEN2)
SHIELD: U2.S1 (SHIELD), U2.S2 (SHIELD), U2.S3 (SHIELD), U2.S4 (SHIELD)

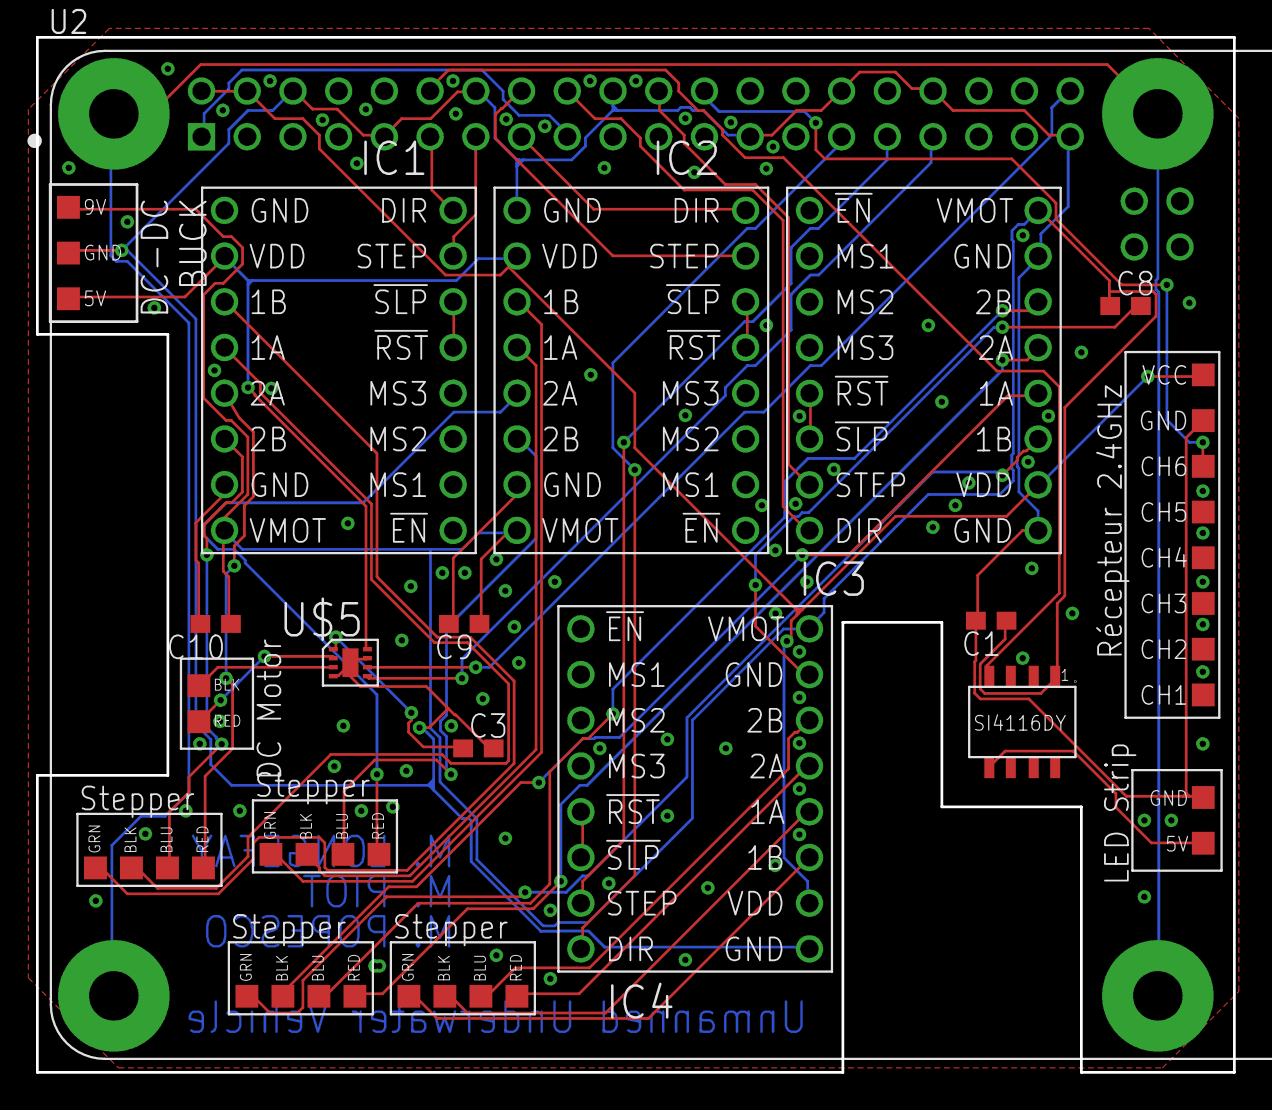
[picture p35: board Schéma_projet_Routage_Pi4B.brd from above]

Board: 2 copper layers, 66.5 x 57.5 mm, 20 parts (0 on the bottom side), 44 nets.

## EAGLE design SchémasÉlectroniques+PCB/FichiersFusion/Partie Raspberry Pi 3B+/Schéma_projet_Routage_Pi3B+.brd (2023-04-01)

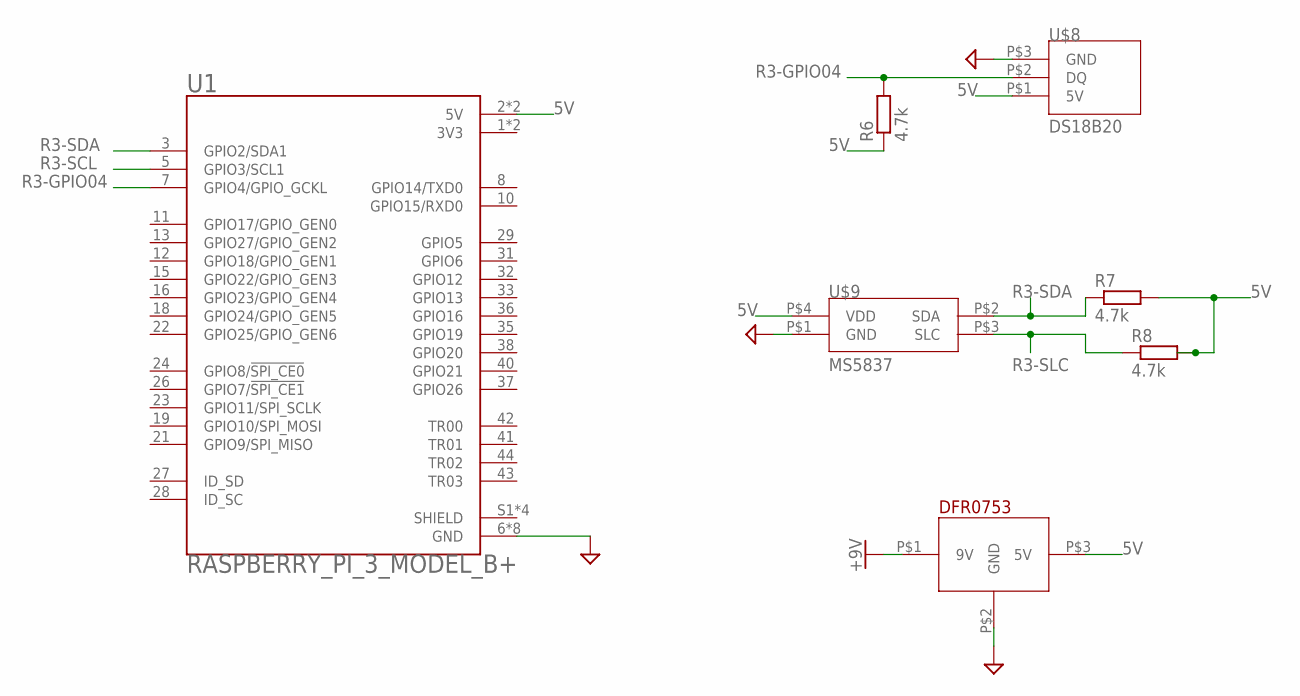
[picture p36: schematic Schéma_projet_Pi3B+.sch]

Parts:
R6, R7, R8: 4.7k; R0603
U1: RASPBERRY_PI_3_MODEL_B+; MODULE_RASPBERRY_PI_3_MODEL_B+
U$8: DS18B20
U$9: MS5837
U$11: DFR0753

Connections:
3V3: U1.1 (3V3), U1.17 (3V3)
5V: R6.1, R7.2, R8.2, U1.2 (5V), U1.4 (5V), U$8.P$1 (5V), U$9.P$4 (VDD), U$11.P$3 (5V)
+9V: U$11.P$1 (9V)
AGND: U1.6 (GND), U1.9 (GND), U1.14 (GND), U1.20 (GND), U1.25 (GND), U1.30 (GND), U1.34 (GND), U1.39 (GND), U$8.P$3 (GND), U$9.P$1 (GND), U$11.P$2 (GND)
R3-GPIO04: R6.2, U1.7 (GPIO4/GPIO_GCKL), U$8.P$2 (DQ)
R3-SCL: U1.5 (GPIO3/SCL1)
R3-SDA: R7.1, U1.3 (GPIO2/SDA1), U$9.P$2 (SDA)
R3-SLC: R8.1, U$9.P$3 (SLC)
SHIELD: U1.S1 (SHIELD), U1.S2 (SHIELD), U1.S3 (SHIELD), U1.S4 (SHIELD)

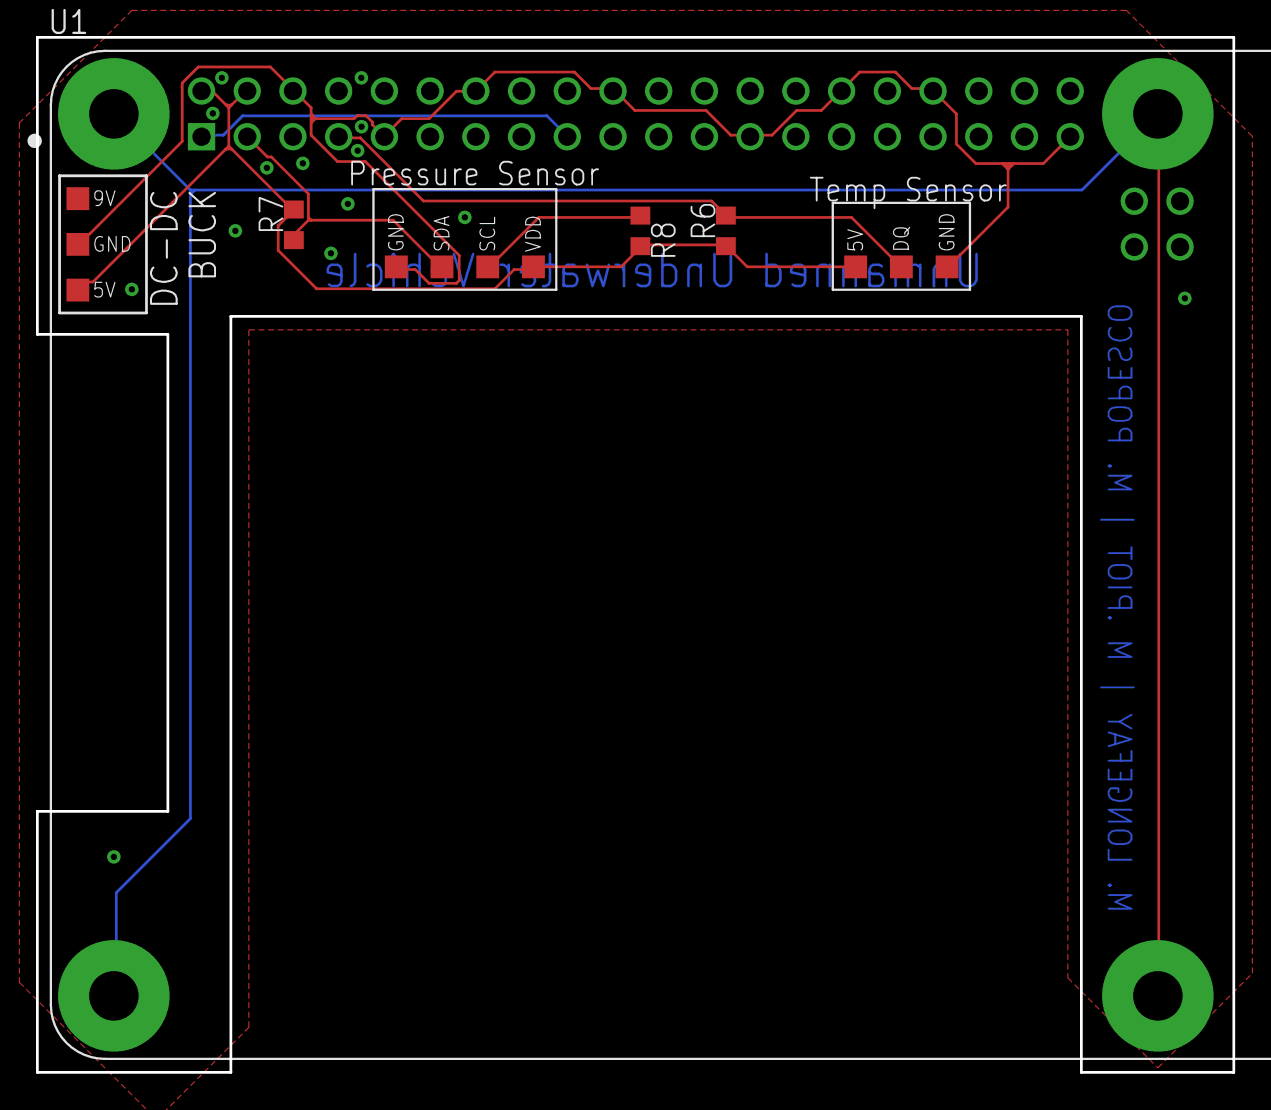
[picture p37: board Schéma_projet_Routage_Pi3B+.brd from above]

Board: 2 copper layers, 66.5 x 57.5 mm, 7 parts (0 on the bottom side), 7 nets.

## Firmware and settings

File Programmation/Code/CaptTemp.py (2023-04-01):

import os
import glob
import time
 
os.system('modprobe w1-gpio')
os.system('modprobe w1-therm')
 
base_dir = '/sys/bus/w1/devices/'
device_folder = glob.glob(base_dir + '28*')
if not device_folder:
    print('Error: No DS18B20 devices found')
    exit(1)
device_folder = device_folder[0]
device_file = device_folder + '/w1_slave'
 
def read_temp_raw():
    f = open(device_file, 'r')
    lines = f.readlines()
    f.close()
    return lines
 
def read_temp():
    lines = read_temp_raw()
    while lines[0].strip()[-3:] != 'YES':
        time.sleep(0.2)
        lines = read_temp_raw()
    equals_pos = lines[1].find('t=')
    if equals_pos != -1:
        temp_string = lines[1][equals_pos+2:]
        temp_c = float(temp_string) / 1000.0
        temp_f = temp_c * 9.0 / 5.0 + 32.0
        return temp_c, temp_f
    
while True:
    temp = read_temp()
    if temp:
        print(temp)
    time.sleep(0.5)

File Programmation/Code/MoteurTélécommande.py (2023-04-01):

import RPi.GPIO as GPIO
from collections import Counter
import time
import threading





#####################################################################################
##                      INITIALIZATION : DATA FROM CONTROLLER                      ##
#####################################################################################

### Initialize all PIN use for get datas from 2.4GHz controller
PIN_CH1 = 12
PIN_CH2 = 19
PIN_CH3 = 16
PIN_CH4 = 26
PIN_CH5 = 20
PIN_CH6 = 8

GPIO.setmode(GPIO.BCM)
GPIO.setup(PIN_CH1, GPIO.IN, pull_up_down = GPIO.PUD_UP)
GPIO.setup(PIN_CH2, GPIO.IN, pull_up_down = GPIO.PUD_UP)
GPIO.setup(PIN_CH3, GPIO.IN, pull_up_down = GPIO.PUD_UP)
GPIO.setup(PIN_CH4, GPIO.IN, pull_up_down = GPIO.PUD_UP)
GPIO.setup(PIN_CH5, GPIO.IN, pull_up_down = GPIO.PUD_UP)
GPIO.setup(PIN_CH6, GPIO.IN, pull_up_down = GPIO.PUD_UP)

### Initialize lists for 10 last values of each get datas
CH1_LastValues = [0]*20
CH2_LastValues = [0]*20
CH3_LastValues = [0]*20
CH4_LastValues = [0]*20
CH5_LastValues = [0]*20
CH6_LastValues = [0]*20

### Initialize main values for the future code (for motors)
CHTable_MainValue = [0]*6
CH1_MainValue = 0
CH2_MainValue = 0
CH3_MainValue = 0
CH4_MainValue = 0
CH5_MainValue = 0
CH6_MainValue = 0

CH3_LastMainValue = 0
CH6_LastMainValue = 0





######################################################################################
##                        INITIALIZATION : CONTROL OF MOTORS                        ##
######################################################################################

### Initialize all PIN use for the control of the different motors
GPIO.setwarnings(False)
## All steppers
Stepper1 = 27 # CH1-CH4
Stepper2 = 23 # CH1-CH4
Stepper3 = 25 # CH2-CH5
Stepper4 = 6  # CH2-CH5
DirectionStepper1 = 17
DirectionStepper2 = 22
DirectionStepper3 = 24
DirectionStepper4 = 5
GPIO.setup(Stepper1, GPIO.OUT)
GPIO.setup(Stepper2, GPIO.OUT)
GPIO.setup(Stepper3, GPIO.OUT)
GPIO.setup(Stepper4, GPIO.OUT)
GPIO.setup(DirectionStepper1, GPIO.OUT)
GPIO.setup(DirectionStepper2, GPIO.OUT)
GPIO.setup(DirectionStepper3, GPIO.OUT)
GPIO.setup(DirectionStepper4, GPIO.OUT)
## DC Motors
DC_PWM = 13
DC_Direction = 21
GPIO.setup(DC_PWM, GPIO.OUT)
GPIO.setup(DC_Direction,GPIO.OUT)
### Define the frequence for the PWM for the DC Motor
DutyCycle = 0
Hz = 1000
PWM = GPIO.PWM(DC_PWM, Hz)

### Initialize PIN for activate or not the LED Strip
PIN_LED = 18
GPIO.setup(PIN_LED, GPIO.OUT)





######################################################################################
#                      INITIALIZATION : STEPPER MOTOR FUNCTIONS                      #
######################################################################################

### Function create to activate or not the motor turning
def ActivateTurn (CHn_MainValue, pinstep):
    if CHn_MainValue == 1 or CHn_MainValue == -1:
        totalSleep = 0.0005
    if CHn_MainValue == 2 or CHn_MainValue == -2:
        totalSleep = 0.0005
    for x in range(10):
        GPIO.output(pinstep, GPIO.HIGH)
        time.sleep(totalSleep)
        GPIO.output(pinstep, GPIO.LOW)
        time.sleep(totalSleep)
        print("vroom")

### The next 2 functions are defined for the Multi-Threading for Stepper Motors
### Goal here is to turn a number of steps clockwise or anti-clockwise at a given speed
def CoupledMotors1(CHTable_MainValue, Stepper1, DirectionStepper1, Stepper3, DirectionStepper3):
    try :
        # CH1 - Yaw movement (rotation [lacet])
        if CHTable_MainValue[0] == 1 and CHTable_MainValue[3] == 0:
            GPIO.output(DirectionStepper1, GPIO.HIGH) #CW
            ActivateTurn(Stepper1)
        elif CHTable_MainValue[0] == -1 and CHTable_MainValue[3] == 0:
            GPIO.output(DirectionStepper1, GPIO.LOW) #CCW
            ActivateTurn(Stepper1)
        else:
            GPIO.output(Stepper1, GPIO.LOW)

        # CH2 - Pitch movement (rotation [tangage])
        if CHTable_MainValue[1] == 1 and CHTable_MainValue[4] == 0:
            GPIO.output(DirectionStepper3, GPIO.HIGH) #CW
            ActivateTurn(Stepper3)
        elif CHTable_MainValue[1] == -1 and CHTable_MainValue[4] == 0:
            GPIO.output(DirectionStepper3, GPIO.LOW) #CCW
            ActivateTurn(Stepper3)
        else:
            GPIO.output(Stepper3, GPIO.LOW)
        
        # CH4 - Straf movement (translation [latteral])
        if CHTable_MainValue[3] == 1:
            GPIO.output(DirectionStepper1, GPIO.HIGH) #CW
            ActivateTurn(Stepper1)
        elif CHTable_MainValue[3] == -1 :
            GPIO.output(DirectionStepper1, GPIO.LOW) #CCW
            ActivateTurn(Stepper1)
        else:
            GPIO.output(Stepper1, GPIO.LOW)

        # CH5 - Depth movement (translation [profondeur])
        if CHTable_MainValue[4] == 0:
            GPIO.output(Stepper3, GPIO.LOW)
        elif CHTable_MainValue[4] == 1:
            GPIO.output(DirectionStepper3, GPIO.HIGH) #CW
            ActivateTurn(Stepper3)
        elif CHTable_MainValue[4] == -1:
            GPIO.output(DirectionStepper3, GPIO.LOW) #CCW
            ActivateTurn(Stepper3)
        else:
            GPIO.output(Stepper3, GPIO.LOW)

    except AttributeError:
        print('AttributeError : Thread1')
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

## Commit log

2023-04-01 Added all project files (1/2)
    All the files needed to redo or continue the project.
    [Aile.sldprt, AileGauche.sldprt, Assemblage1.sldasm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]
2023-04-01 Added all project files (2/2)
    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
    [Schéma_projet_Pi3B+.sch, Schéma_projet_Pi4B.sch, Schéma_projet_Routage_Pi3B+.brd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]
